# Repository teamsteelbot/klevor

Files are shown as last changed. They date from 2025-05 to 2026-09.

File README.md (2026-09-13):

# Klevor

> [!NOTE]
> Este repositorio corresponde a nuestra participación en la World Robot Olympiad 2025. Si buscas información sobre nuestra participación en la World Robot Olympiad 2026 con V-Titan, el robot del Team Voltimor, visita el repositorio [**vtitan**](https://github.com/teamvoltimor/vtitan).

> [!IMPORTANT]
> If you want to access this content in English, click [**here**](README-en.md)

<p align="center">
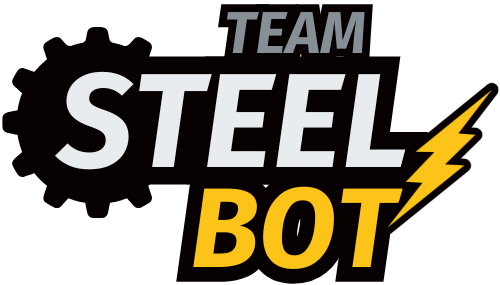
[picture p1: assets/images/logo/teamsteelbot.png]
Logo del Equipo
    
    <br>
    <i>Logo del Equipo</i>
</p>

Bienvenidos al repositorio de Klevor, el robot del Team Steel Bot, que compite en la World Robot Olympiad 2025 en la categoría Futuros Ingenieros. Aquí encontrarás toda la información sobre el robot, incluyendo su código, modelos 3D, esquemas y documentación.

## ¿Cómo acceder a la documentación?

Actualmente, toda la documentación oficial se encuentra tanto en [GitHub Pages](https://klevor.ralvarez.dev), como en el repositorio de [GitHub](https://github.com/teamsteelbot/klevor), recomendamos visualizarla en GitHub Pages, ya que esta documentación fue desarrollada para encajar mejor en este formato. Esta documentación está organizada en varias secciones, cada una de las cuales contiene información específica sobre el robot y su desarrollo.

<p align="center">
	Código QR de la URL de la página web
	<br>
	<i>Código QR de la URL de la página web</i>
</p>

<p align="center">
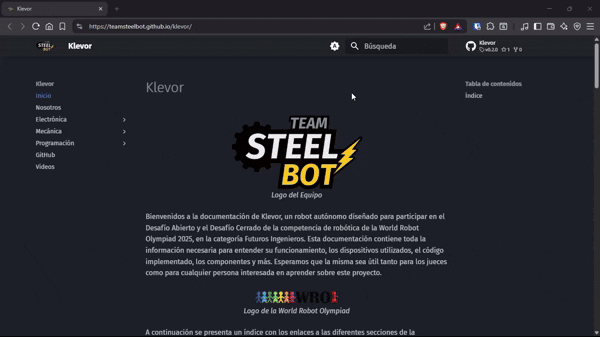
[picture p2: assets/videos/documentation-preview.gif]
Preview de la documentación en GitHub Pages
	
	<br>
	<i>Preview de la documentación en GitHub Pages</i>
</p>

## Estructura de la documentación

Esta documentación es bastante extensa, por lo que decidimos dividir los contenidos de esta documentación en múltiples archivos para facilitar la lectura, los cuales están ubicados en la carpeta `docs`; cabe recalcar que, si un archivo termina en `.es.md` está escrito en español, y si termina en `.en.md` está escrito en inglés.

Ahora bien, la estructura de los archivos es la siguiente:

- En la carpeta `assets` se encuentran las imágenes y videos que utilizamos para este `README`.

- En la carpeta `devices` se encuentra todo el código utilizado por Klevor, dividido en dos carpetas, una para la Raspberry Pi 5, y la otra para la Raspberry Pi Pico 2 W.

- En la carpeta `docs`, como ya se ha mencionado, se encuentra todo lo documentado sobre Klevor, dividido en 3 secciones, la electrónica, la mecánica, la programación, además de estas secciones, también contamos con algunos archivos que detallan, por ejemplo, el software utilizado, los "gadgets" o herramientas que utilizamos, cómo nos pueden contactar, y demás, **estos archivos están listados al final del índice**.

- En la carpeta `models` se encuentran todos los modelos de las piezas 3d que fueron impresas para Klevor, esta carpeta está dividida para los planos de las piezas, y el archivo para imprimirlas, además de, estar organizadas por cada prototipo.

- En la carpeta `schemes` están los diagramas de flujo, y los diagramas de conexiones, además de esto, se incluyeron unos diagramas que explican cómo funciona el sistema de comunicación entre los componentes de Klevor y como se procesan en la Raspberry Pi.

- En la carpeta `t-photos` están las fotos del equipo.

- En la carpeta `v-photos` están las fotos de Klevor.

## Índice 

1. **[Sobre Nosotros](docs/about.es.md)**
2. **Electrónica**
	1. Componentes
		1. [Componentes Previos](docs/electronic/components/previous.es.md)
		2. [Componentes Actuales](docs/electronic/components/current.es.md)
		3. [Componentes Futuros](docs/electronic/components/future.es.md)
	2. Diagramas
		1. [Diagramas de Conexiones](docs/electronic/diagrams/wiring.es.md)
3. **Mecánica**
	1. Piezas
		1. Piezas Comunes
			1. [Piezas Comunes Previas](docs/mechanical/parts/common/previous.es.md)
			2. [Piezas Comunes Actuales](docs/mechanical/parts/common/current.es.md)
		2. [Piezas del Prototipo 1](docs/mechanical/parts/prototype1.es.md)
		3. [Piezas del Prototipo 2](docs/mechanical/parts/prototype2.es.md)
		4. [Piezas del Prototipo 3](docs/mechanical/parts/prototype3.es.md)
		5. [Piezas del Prototipo 4](docs/mechanical/parts/prototype4.es.md)
	2. Prototipos
		1. [Prototipo 1](docs/mechanical/prototypes/prototype1.es.md)
		2. [Prototipo 2](docs/mechanical/prototypes/prototype2.es.md)
		3. [Prototipo 3](docs/mechanical/prototypes/prototype3.es.md)
		4. [Prototipo 4](docs/mechanical/prototypes/prototype4.es.md)
4. **Programación**
	1. Lenguajes de Programación
		1. [Lenguajes de Programación Previos](docs/programming/languages/previous.es.md)
		2. [Lenguajes de Programación Actuales](docs/programming/languages/current.es.md)
		3. [Lenguajes de Programación Futuros](docs/programming/languages/future.es.md)
	2. Librerías
		1. Legado:
		   1. [Librerías de CircuitPython](docs/programming/libraries/legacy/circuit-python.es.md)
		2. [Librerías de Python](docs/programming/libraries/python.es.md)
	3. Diagramas
		1. [Diagramas de Flujo](docs/programming/diagrams/flowcharts.es.md)
	4. [Glosario de Términos](docs/programming/glossary.es.md)
	5. Guías
		1. Legado 
			1. [Guía de MicroPython](docs/programming/guides/legacy/micro-python.es.md)
			2. [Guía de CircuitPython](docs/programming/guides/legacy/circuit-python.es.md)
			3. [Guía de la Raspberry Pi Pico 2 W](docs/programming/guides/legacy/raspberry-pi-pico-2w.es.md)
		2. [Guía de MkDocs](docs/programming/guides/mkdocs.es.md)
		3. [Guía de TinyGo](docs/programming/guides/tinygo.es.md)
		4. [Guía de la Raspberry Pi 5](docs/programming/guides/raspberry-pi-5.es.md)
		5. [Guía de la Raspberry Pi Pico 2 W](docs/programming/guides/raspberry-pi-pico-2w.es.md)
		6. [Guía de Detección de Objetos](docs/programming/guides/object-detection.es.md)
5. **[GitHub](docs/github.es.md)**
6. **[Vídeos](docs/videos.es.md)**
7. **[Software](docs/software.es.md)**
8. **[Gadgets](docs/gadgets.es.md)**
9. **[Patrocinadores](docs/sponsors.es.md)**
10. **[Contacto](docs/contact.es.md)**

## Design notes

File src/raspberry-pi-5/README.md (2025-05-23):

<h1 id="indice">Índice</h1>

1. [Configuración Básica de la Raspberry Pi](#configuracion-basica-de-la-raspberry-pi)
   1. [Instalación de Raspberry Pi OS](#instalacion-de-raspberry-pi-os) 
   2. [Instalación de la cámara](#instalacion-de-la-camara)
2. [Multiprocesamiento](#multiprocesamiento)
3. [YOLO](yolo/README.md)
4. [Recursos Externos](#recursos-externos)

<h1 id="configuracion-basica-de-la-raspberry-pi">Configuración Básica de la Raspberry Pi</h1>

<h1 id="instalacion-de-raspberry-pi-os">Instalación de Raspberry Pi OS</h1>

1. Descargar la imagen de Raspberry Pi OS desde el sitio oficial: [Raspberry Pi OS](https://www.raspberrypi.com/software/).
2. Grabar la imagen en una tarjeta microSD utilizando un software como Balena Etcher o Raspberry Pi Imager.
3. Insertar la tarjeta microSD en la Raspberry Pi y encenderla.
4. Configurar la Raspberry Pi siguiendo las instrucciones en pantalla, incluyendo la conexión a una red Wi-Fi y la creación de un usuario.
5. Actualizar el sistema operativo ejecutando los siguientes comandos en la terminal:
   ```bash
   sudo apt update
   sudo apt upgrade
   ```
   
<p align="center">
    Raspberry Pi OS
    <br>
    <i>Raspberry Pi OS</i>
</p>

*TIP: Por experiencia propia, recomendamos la configuración de la aplicación oficial de Raspberry Pi para conexión remota, Raspberry Pi Connect, que permite acceder a la Raspberry Pi desde cualquier lugar y sin necesidad de estar conectado a la misma red Wi-Fi [[3](#raspberry-pi-connect)]. En nuestro caso, en reiteradas ocasiones nos permitió de forma remota, a través del modo Remote Shell, eliminar procesos que han producido un crash o han limitado la repuesta de la Raspberry Pi.* 

<h1 id="instalacion-de-la-camara">Instalación de la cámara</h1>

1. Conectar la cámara a la Raspberry Pi utilizando el conector CSI.
2. Probar el correcto funcionamiento de la cámara ejecutando el siguiente comando en la terminal:
   ```bash
   libcamera-hello
   ```
3. Si la cámara funciona correctamente, se mostrará una vista previa de la cámara en la pantalla por unos segundos.

*NOTA: En caso de estar interesado en adquirir algún tipo de Raspberry Pi Camera, se debe comprar un cable aparte dependiendo del proveedor, ya que normalmente estas vienen con el cable para la Raspberry Pi 4, el cual no es el mismo.*

<h1 id="multiprocesamiento">Multiprocesamiento</h1>

<h1 id="recursos-externos">Recursos Externos</h1>

1. *Raspberry Pi OS*. (2025). Raspberry Pi. <a id="raspberry-pi-os">https://www.raspberrypi.com/software/</a>
2. *Getting Started*. (2025). Raspberry Pi. <a id="getting-started">https://www.raspberrypi.com/documentation/getting-started/</a>
3. *Raspberry Pi Connect*. (2025). Raspberry Pi. <a id="raspberry-pi-connect">https://www.raspberrypi.com/documentation/remote-access/raspberry-pi-connect.html</a>
4. Python Software Foundation. (2025). *Multiprocessing*. Python documentation. <a id="multiprocessing">https://docs.python.org/3/library/multiprocessing.html</a>
5. Brownlee, J. (28 de julio de 2022). *Use an Event in the Multiprocessing Pool*. SuperFastPython*. <a id="multiprocessing-pool">https://superfastpython.com/multiprocessing-pool/</a>
6. *Camera*. (2025). Raspberry Pi. <a id="camera">https://www.raspberrypi.com/documentation/computers/camera.html</a>
7. Brownlee, J. (21 de noviembre de 2022). *What is a Multiprocessing Manager*. SuperFastPython. <a id="multiprocessing-manager">https://superfastpython.com/multiprocessing-manager/</a>

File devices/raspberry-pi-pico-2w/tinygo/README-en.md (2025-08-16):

# Code

This folder contains all the code developed in TinyGo for the development of Klevor. It is recommended to use a Raspberry Pi Pico 2 WH (although any microcontroller with TinyGo should work with some adjustments) to run the files.

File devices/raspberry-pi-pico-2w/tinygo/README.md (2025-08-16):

# Código

Esta carpeta tiene todo el código realizado en TinyGo para el desarrollo de Klevor, se recomienda utilizar una Raspberry Pi Pico 2 WH (aunque, cualquier microcontrolador con TinyGo debería de poder funcionar si se realizan ciertos ajustes) para poder ejecutar los archivos.

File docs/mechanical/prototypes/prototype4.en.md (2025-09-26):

# Prototype 4

## Vehicle Photos

<!-- github-only-start -->
<table>
	<tbody>
		<tr>
			<td>
				<p align="center">
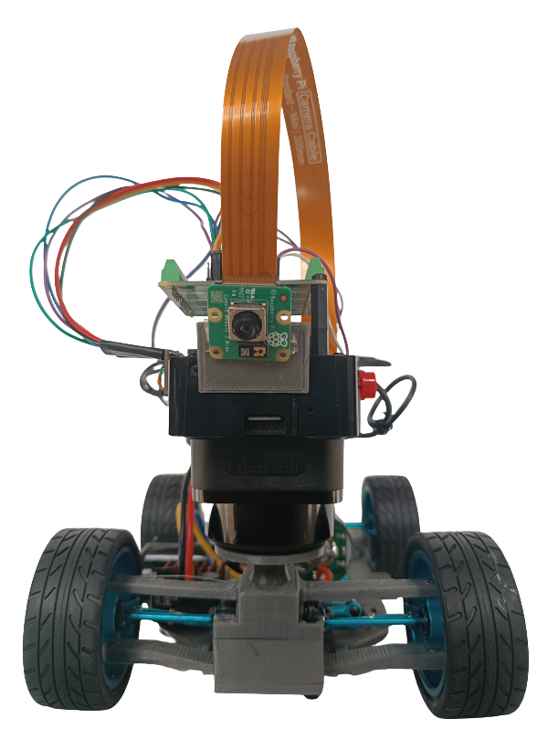
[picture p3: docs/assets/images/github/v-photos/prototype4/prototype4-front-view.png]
Front View
					
					<br>
					<i>Front View</i>
				</p>
			</td>
			<td>
				<p align="center">
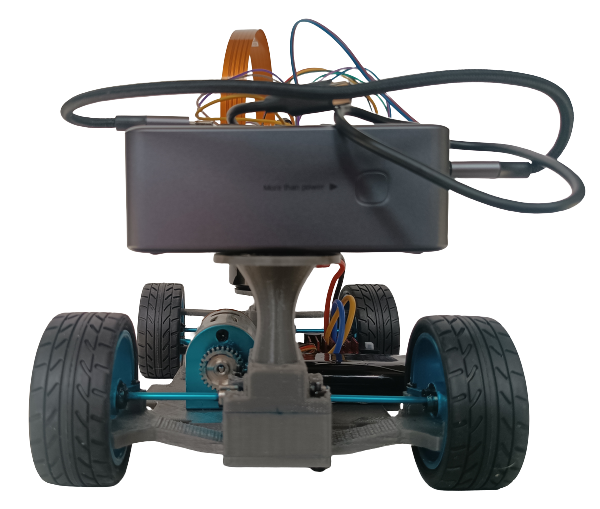
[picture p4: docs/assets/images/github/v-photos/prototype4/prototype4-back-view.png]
Back View
					
					<br>
					<i>Back View</i>
				</p>
			</td>
		</tr>
		<tr>
			<td>
				<p align="center">
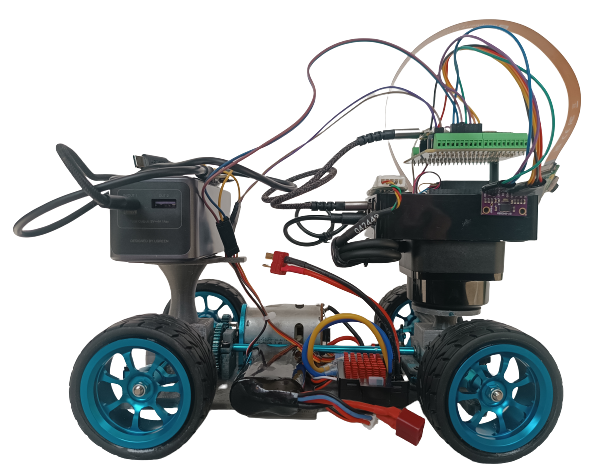
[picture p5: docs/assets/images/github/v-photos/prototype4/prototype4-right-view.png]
Right View
					
					<br>
					<i>Right View</i>
				</p>
			</td>
			<td>
				<p align="center">
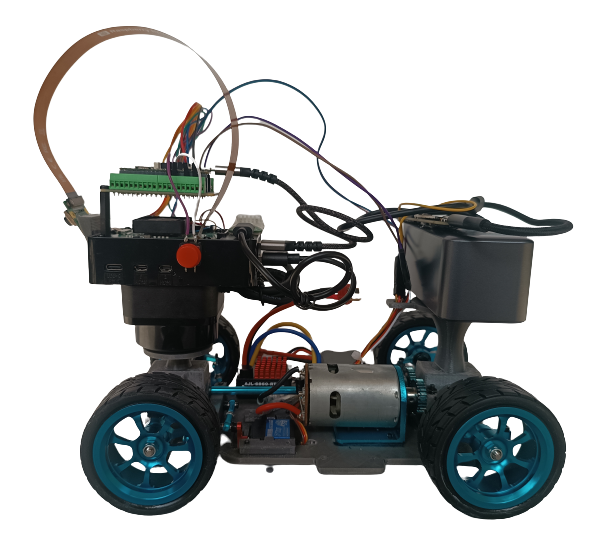
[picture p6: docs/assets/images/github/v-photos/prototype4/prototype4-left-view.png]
Left View
					
					<br>
					<i>Left View</i>
				</p>
			</td>
		</tr>
		<tr>
			<td>
				<p align="center">
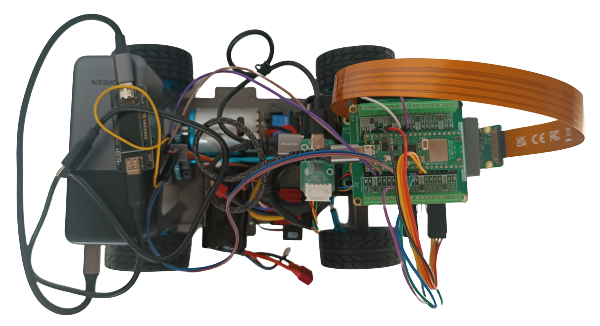
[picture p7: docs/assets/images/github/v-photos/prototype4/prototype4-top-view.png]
Top View
					
					<br>
					<i>Top View</i>
				</p>
			</td>
			<td>
				<p align="center">
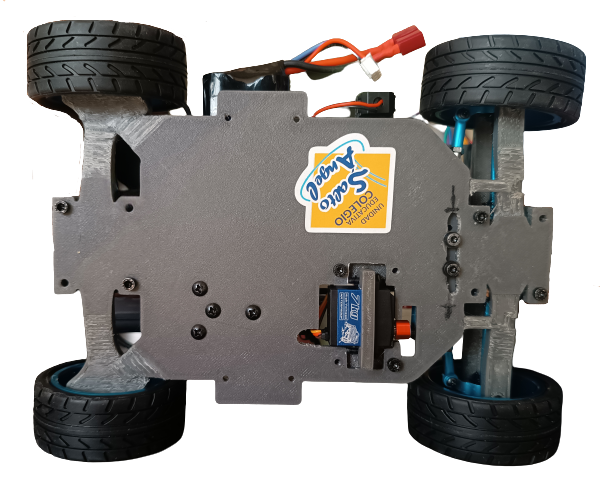
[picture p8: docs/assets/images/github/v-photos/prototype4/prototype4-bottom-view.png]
Bottom View
					
					<br>
					<i>Bottom View</i>
				</p>
			</td>
		</tr>
	</tbody>
</table>
<!-- github-only-end -->

<!-- mkdocs-only-start
<div class="vehicle-views-container">
    <div class="hcenter">
        <img src="/assets/images/github/v-photos/prototype4/prototype4-front-view.png" 
alt="Front View" class="vehicle-view-image">
        <i>Front View</i>
    </div>
    <div class="hcenter">
        <img src="/assets/images/github/v-photos/prototype4/prototype4-back-view.png" 
alt="Back View" class="vehicle-view-image">
        <i>Back View</i>
    </div>
    <div class="hcenter">
        <img src="/assets/images/github/v-photos/prototype4/prototype4-right-view.png" 
alt="Right View" class="vehicle-view-image">
        <i>Right View</i>
    </div> 
    <div class="hcenter">
        <img src="/assets/images/github/v-photos/prototype4/prototype4-left-view.png" 
alt="Left View" class="vehicle-view-image">
        <i>Left View</i>
    </div>
    <div class="hcenter">
        <img src="/assets/images/github/v-photos/prototype4/prototype4-top-view.png"
alt="Top View" class="vehicle-view-image">
        <i>Top View</i>
    </div>
    <div class="hcenter">
        <img src="/assets/images/github/v-photos/prototype4/prototype4SS-bottom-view.png" 
alt="Bottom View" class="vehicle-view-image">
        <i>Bottom View</i>
    </div>
</div>
mkdocs-only-end -->

## Introduction

This Klevor prototype is the fruit of labor focused on improving its efficiency to complete the challenges that this WRO edition provides. Across these upgrades, we prioritized the mechanical engineering to overcome the limitations from previous prototypes and optimized its performance.

From the very first concept, Klevor was born with a clear idea. It was established that its main processor would be a Raspberry Pi 5, a decision that made us able to add Artificial Intelligence capabilities with an AI HAT+ and a Raspberry Pi Cam 3 to detect precisely the object. For the navigation, we used the RPLiDAR C1 sensor, which provides a detection from multiple angles.

Klevor uses a 4x4 traction system to maximize the strength and control. Also, we implemented a Ackermann steering system, which optimizes the wheels' turning angle. This system, known for its use in automobiles, aligns the turning wheels in a way that all of them turn around a common point, which mainly improves the stability during the turns.

To build our robot's unique parts, such as the bases and supports, we used a design program named Fusion360. With this program we were able to create every single piece from scratch and then 3D print them. Thanks to this, we could have less margin for errors, or correct quicker, achieving a more optimal design.

Thorought this prototype's explanation, we will detail in Klevor's trayectory, starting from the component's first ideas to the creation of solutions that helped with our problems related to power, traction and weight.

Another fundamental part for our robot is its crossing system, which consists of a servomotor ([INJORA 7 kg 2065](../../electronic/components/current.en.md#injora-7-kg-2065-micro-servo)) which is connected to our "Ackermann" system that works by connecting both wheels to a steering or "trapezoid system". The servomotor moves some bars that are connected to the steering knuckles, thus allowing that one of the steering knuckles to be pushed to one side by the movement of the servomotor and in turn, pull the other wheel to the other side. Due to the angles of the trapezoid, this causes that the interior wheel to turn more than the outer one.

To operate, the wheels are connected to a steering knuckle, then to a "shaft" or "half-shaft" that passes through the knuckle and joins the wheel so that it turns; the shaft turns while it is next to the differential.

<!-- github-only-start -->
<p align="center">
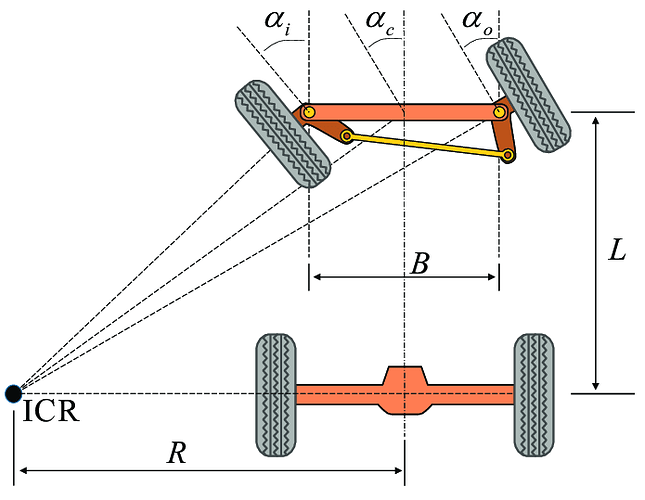
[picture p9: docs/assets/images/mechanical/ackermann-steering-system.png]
Ackermann System
    
    <br>
    <i>Ackermann System</i>
</p>
<!-- github-only-end -->

<!-- mkdocs-only-start
<div class="hcenter">
    <img src="/assets/images/mechanical/ackermann-steering-system.png" 
alt="Ackermann System" class="mechanical-image">
    <i>Ackermann System</i>
</div>
mkdocs-only-end -->

This diagram provides a clearer example on how this system works. We'll describe the meaning of each term below:

- **ICR** (Instantaneous Center of Rotation): It's the point around which the front axle is rotating.

- **R**: It's the vehicle's turning radius, measured from the ICR to the center of the rear axle.

- **L**: It's the distance between the front and rear axle, or, the transmission shaft's length.

- **B**: It's the distance between the sterring knuckles (The piece on which the wheel goes and is connected to the steering).

- **a(i)**: Is the turning angle of our inner wheel compared to the curve.

- **a(o)**: Is the angle of our outer wheel with respect to the turn.

This ilustrates better the steering geometry that allows for the front wheels to turn in different angles and, at the same time, achieving a more efficient turning.

## Changes

To improve Klevor's performance and efficiency, we implemented multiple changes in its design. These upgrades are focused in upgrading aspects such as traction, motor power and weight distribution.

- New chassis and wheels

Klevor's new chassis was designed specifically to integrate the new components, assuring that each of them has the adequate space for its proper functioning. The main reason for this redesign was the incorporation for new aluminum wheels. Unlike previous prototypes, these wheels have a larger diameter and are wider, their tire rubber is also thicker and smoother. This design provides a better grip on flat surfaces, correcting traction problems that we had previously.

- Bigger torque and motor efficiency

We replaced the previous motor (INJORA 48T) with another motor that has more torque. This change allows us to use the motor's speed to its fullest, which is worth noting, since it can go above the 20,000 RPM, without the need of a system to reduce the revolutions per minute (RPM).

- Weight reduction

Another significant change is that we substituted the power supply. In previous prototypes, we used a power bank and weighted almost 600g (Shargeek Storm 2), which limitated our ability to modify the design. Now, with a new power bank weighing just 350g, we have achieved a considerable weight reduction. This upgrade allows us to have more freedom to optimize the chassis without having to worry about the robot's weight.

## How did we design Klevor?

First of all, we think, "What do we need to get an efficient robot?" Starting from there, we established a clear idea, a robot programmed with a Raspberry Pi 5, which would allow us to use a Raspberry Pi AI HAT+ and train our Raspberry Pi Cam 3 through artificial intelligence, which would definitely help us have a better performance in the Closed Challenge, and, to make sure Klevor detects the objects surrounding it, capable to detect with a wide range, we decided to use the RPLiDAR C1 since our second prototype. Mechanically wise, we always wanted to use a 4x4 traction system and Ackermann's steering geometry.

To make everything work, we thought about every component we wanted to use, to build mountings and supports for them, we decided that it was a good idea to 3D print these supports, more specifically, we used PETG filament, which is very resistant, affordable and easy to come by, which would allow us to make multiple tests.

All of our 3D printed parts were created from scratch, designed in a program called Fusion360, this same program was a huge help in multiple aspects, for example, we could simulate the dimensions from each component in the program and then afterwards create multiple designs for the chassis.

## Problems and solutions during developmennt

Even though we had a solid idea as to how we wanted to shape Klevor, we had a few inconveniences during the building process, for Klevor's first 3 prototypes we decided to use a Motor Injora 48T, which we thought it could move the whole robot, even thought it was a 20000 RPM motor, it didn't have enough torque to move Klevor, so we created a RPM reduction system, according to these principles:

**When a smaller pinion (impulsor) moves a bigger pinion (impulsed), the speed decreases and the torque increases.**

**When a bigger pinion (impulsor) moves a smaller pinion (impulsed), the torque decreases and the speed increases.**

**The reduction ratio or transmission ratio can be calculated with the following formula:**

<!-- github-only-start -->
<p align="center">
	Gear Ratio Formula
	<br>
	<i>Gear Ratio Formula</i>
</p>
<!-- github-only-end -->

<!-- mkdocs-only-start
<div class="hcenter">
	<img src="/assets/images/mechanical/gear-ratio-formula.png" alt="Gear Ratio Formula" class="mechanical-image">
	<i>Gear Ratio Formula</i>
</div>
mkdocs-only-end -->

This means that, in order to increase the torque, we have to arrange the system in a way that, pinions with less teeth are the ones that move pinions with more teeth, this was the solution to our torque problem.

Afterwards, we had to make Klevor lighter, the reason for this change, were the previously mentioned, new wheels, because the old wheels' rims were 3D printed, which in turn, wore them down quickly. The newer wheels had an aluminum rim and a thicker rubber, which in tunr, would make Kleovr exceed the reglamentary weight limit established by the WRO, what we did to solve this problem and to make the robot faster as well, was to change the motor, with one that had 20000 RPM, but with enough torque, which made the RPM reduction system obsolete.

Another issue that was present during Klevor's development was its limited turning angle, which supposed a huge challenge in the game field. To correct it, we modified the shape of the Ackermann steering system, which is composed of two direction knuckles and the shaft that unifies them, by adjusting the position and angle of these components, we increased Klevor's turning angle significantly.

## Bill Of Materials

| Component |  Unit  | Cost per Unit ($)  | Total ($) |
|---|---|---|---|
| [Raspberry Pi 5](https://www.canakit.com/raspberry-pi-5-16gb.html) | 1 | 120.00 | 120.00 |
| [Raspberry Pi AI HAT+](https://www.canakit.com/raspberry-pi-ai-hat-with-case.html) | 1 | 139.95 | 139.95 |
| [Micro SD 512GB](https://www.amazon.com/dp/B0C1Q79X3P) | 1 | 54.99 | 54.99 |
| [RPLiDAR C1](https://www.amazon.com/dp/B0CNXLJJ61) | 1 | 75.90 | 75.90 |
| [Raspberry Pi Camera Module 3 Wide](https://www.canakit.com/raspberry-pi-camera-module-3.html) | 1 | 37.95 | 37.95 |
| [Case para la Raspberry Pi Camera Module 3](https://www.amazon.com/dp/B09TNG4V55) | 1 | 5.99 | 5.99 |
| [Cable para la cámara de la Raspberry Pi 5 de 50cm](https://www.amazon.com/dp/B0D3YWTNF8) | 1 | 9.79 | 9.79 |
| [Raspberry Pi Pico 2WH](https://www.amazon.com/dp/B0F4W9J5CC) | 1 | 14.99 | 14.99 |
| [Raspberry Pi Pico 2WH Breakout Board](https://www.amazon.com/dp/B0BFB53Y2N) | 1 | 11.95 | 11.95 |
| [URGENEX 3000mAh Battery](https://www.amazon.com/dp/B0CYNVSN7W) | 1 | 26.99 | 26.99 |
| [Giroscopio BNO085](https://www.amazon.com/dp/B0CDGZMLPP) | 1 | 18.59 | 18.59 |
| [INJORA 7Kg 2065 Servo](https://www.amazon.com/dp/B0BLBMVYCW) | 1 | 17.98 | 17.98 |
| [60A Brushed ESC para 2-3s LiPo y motor 540](https://www.amazon.com/dp/B0F9Y6CMC8) | 1 | 15.98 | 15.98 |
| [Motor 540 y disipador de calor de aluminio](https://www.amazon.com/dp/B0995W966Z) | 1 | 19.39 | 19.39 |
| [UGREEN Power Bank 12000mAh 100W PD PPS](https://www.amazon.com/dp/B0CXJ1F1M7) | 1 | 49.99 | 49.99 |
| [Aluminium Alloy Front & Rear Steering Knuckle Hub Base](https://www.amazon.com/dp/B09XW246FQ) | 1 | 17.99 | 17.99 |
| [RC Car Metal Differential Kit 1/18](https://www.amazon.com/dp/B08GHC4D5M) | 1 | 21.98 | 21.98 |
| [USB-C QC PD3.0 Trigger Board Module Type-C](https://www.amazon.com/dp/B0DRJWBG7G) | 1 | 16.99 | 16.99 |
| [Llantas de metal con buje de metal de 0.472 pulg](https://www.amazon.com/dp/B0BP2W7W59) | 1 | 20.99 | 20.99 |
| [Copa diferencial de aleación de aluminio y junta de eje de transmisión](https://www.amazon.com/dp/B09P1QV29K) | 1 | 10.99 | 10.99 |
| [20 rodamientos de bolas MR128-2RS](https://www.amazon.com/dp/B09P1QV29K) | 1 | 9.29 | 9.29 |
| [Uxcell 0.276 in I.D. Rodamientos de bolas en miniatura](https://www.amazon.com/dp/B07XYPLPFL) | 1 | 8.49 | 8.49 |
| [Smays Cable USB C de 240 W, cable corto de 1 pie C a C](https://www.amazon.com/dp/B0CYT6KQTR) | 1 | 7.99 | 7.99 |
| [Hobbypark Adaptador hexagonal de rueda de aluminio](https://www.amazon.com/dp/B07D67VMDN) | 1 | 9.97 | 9.97 |
| [6 piezas ajustables de aluminio Hobbypark enlace servo](https://www.amazon.com/dp/B01MQOA4CH) | 1 | 15.95 | 15.95 |
| [6 HobbyPark Metal Diff diferencial engranaje principal 42T y piñón motor 27T](https://www.amazon.com/dp/B07FS5RGLS) | 1 | 11.98 | 11.98 |
| [Cable micro USB corto de 1 pie [paquete de 3]](https://www.amazon.com/dp/B07FS5RGLS) | 1 | 6.99 | 6.99 |

**Component Cost Total: $780.03**

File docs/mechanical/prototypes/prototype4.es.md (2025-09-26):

# Prototipo 4 {:#prototype4}

## Fotos del vehículo

<!-- github-only-start -->
<table>
	<tbody>
		<tr>
			<td>
				<p align="center">
					Vista delantera del prototipo 4
					<br>
					<i>Vista delantera del prototipo 4</i>
				</p>
			</td>
			<td>
				<p align="center">
					Vista trasera del prototipo 4
					<br>
					<i>Vista trasera del prototipo 4</i>
				</p>
			</td>
		</tr>
		<tr>
			<td>
				<p align="center">
					Vista derecha del prototipo 4
					<br>
					<i>Vista derecha del prototipo 4</i>
				</p>
			</td>
			<td>
				<p align="center">
					Vista izquierda del prototipo 4
					<br>
					<i>Vista izquierda del prototipo 4</i>
				</p>
			</td>
		</tr>
		<tr>
			<td>
				<p align="center">
					Vista superior del prototipo 4
					<br>
					<i>Vista superior del prototipo 4</i>
				</p>
			</td>
			<td>
				<p align="center">
					Vista inferior del prototipo 4
					<br>
					<i>Vista inferior del prototipo 4</i>
				</p>
			</td>
		</tr>
	</tbody>
</table>
<!-- github-only-end -->

<!-- mkdocs-only-start
<div class="vehicle-views-container">
    <div class="hcenter">
        <img src="/assets/images/github/v-photos/prototype4/prototype4-front-view.png" 
alt="Vista delantera" class="vehicle-view-image">
        <i>Vista delantera</i>
    </div>
    <div class="hcenter">
        <img src="/assets/images/github/v-photos/prototype4/prototype4-back-view.png" 
alt="Vista Trasera" class="vehicle-view-image">
        <i>Vista trasera</i>
    </div>
    <div class="hcenter">
        <img src="/assets/images/github/v-photos/prototype4/prototype4-right-view.png" 
alt="Vista derecha" class="vehicle-view-image">
        <i>Vista derecha</i>
    </div>
    <div class="hcenter">
        <img src="/assets/images/github/v-photos/prototype4/prototype4-left-view.png" 
alt="Vista izquierda" class="vehicle-view-image">
        <i>Vista izquierda</i>
    </div>
    <div class="hcenter">
        <img src="/assets/images/github/v-photos/prototype4/prototype4-top-view.png"
alt="Vista superior" class="vehicle-view-image">
        <i>Vista superior</i>
    </div>
    <div class="hcenter">
        <img src="/assets/images/github/v-photos/prototype4/prototype4SS-bottom-view.png" 
alt="Vista inferior" class="vehicle-view-image">
        <i>Vista inferior</i>
    </div>
</div>
mkdocs-only-end -->

## Introducción

Este prototipo de Klevor es el fruto de un arduo trabajo enfocado en mejorar su eficiencia a la hora de realizar los desafíos que depara esta edición de la WRO. A lo largo de estas mejoras, hemos priorizado la ingeniería mecánica para superar las limitaciones de prototipos anteriores y optimizar su desempeño.

Desde el primer concepto, Klevor fue pensado con una idea clara. Se estableció que su cerebro sería una Raspberry Pi 5, una decisión que nos permitió añadir capacidades de inteligencia artificial con un AI HAT+ y una Raspberry Pi Cam 3 para la detección precisa de objetos. Para la navegación, utilizamos el sensor RPLidar C1, que proporciona una detección en múltiples ángulos.

Klevor utiliza un sistema de tracción 4x4 para maximizar la fuerza y el control. Además, implementamos un sistema de cruce Ackermann, que optimiza el ángulo de giro de las ruedas. Este sistema, conocido por su uso en automóviles, alinea las ruedas de dirección de manera que todas giren alrededor de un punto común, lo que principalmente mejora la estabilidad durante los giros.

Para construir las partes únicas de nuestro robot, como las bases y los soportes, usamos un programa de diseño llamado Fusion360. Con este programa, pudimos crear cada pieza desde cero y luego imprimirlas en 3D. Gracias esto, pudimos tener menos margen de error, o corregir más rapido, logrando un diseño óptimo.

A lo largo la explicación de este prototipo, detallaremos el trayecto de Klevor, desde las primeras ideas de sus componentes hasta la creación de soluciones que ayudaron con nuestros problemas de potencia, tracción y peso.

Una parte fundamental para nuestro robot es su sistema de cruce. Es basado en un mecanismo Ackermann, que consiste en que las dos ruedas están conectadas por una dirección o "sistema de trapecio", esto lo que hace es que, mediante una fuerza que haga el cruce (en este caso nuestro servomotor [INJORA 7 kg 2065](../../electronic/components/current.md#injora-7kg-2065-micro-servo))la dirección se mueva y eso hace girar ambas ruedas al mismo lado, debido a la geometría y forma de trapecio que tiene la dirección, las ruedas no giran con el mismo ángulo, sino que, la rueda interna respecto al cruce gira más que la rueda externa.

Las ruedas para funcionar están conectadas a un muñón de dirección, luego a un "palier" o "semieje" que pasa por dentro del muñón y se junta con la rueda para que esta gire, el palier gira mientras está junto al diferencial.

<!-- github-only-start -->
<p align="center">
    Sistema de Ackermann
    <br>
    <i>Sistema de Ackermann</i>
</p>
<!-- github-only-end -->

<!-- mkdocs-only-start
<div class="hcenter">
    <img src="/assets/images/mechanical/ackermann-steering-system.png" 
alt="Sistema de Ackermann" class="mechanical-image">
    <i>Sistema de Ackermann</i>
</div>
mkdocs-only-end -->

En este diagrama se ve un ejemplo más claro de cómo funciona este sistema. Describiremos a continuación el significado de cada término:

- **ICR** (Centro Instantáneo de Rotación): Es el punto alrededor del cual el eje delantero está girando.

- **R**: Es el radio del giro del vehículo, medido desde el ICR hasta el centro del eje trasero.

- **L**: Es la distancia entre el eje delantero y el eje trasero de Klevor, o la distancia de nuestro eje transmisor.

- **B**: Es la distancia entre los muñones de dirección (La pieza en la que va la rueda y se conecta a la dirección).

- **a(i)**: Es el ángulo de giro de nuestra rueda interior respecto a la curva.

- **a(o)**: Es el ángulo de nuestra rueda exterior respecto al giro.

Esto ilustra más la geometría de la dirección que permite que las ruedas delanteras giren en ángulos diferentes y a su vez en la misma dirección, consiguiendo así un giro eficiente.

## Cambios
Para mejorar el rendimiento y la eficiencia de Klevor, hemos implementado varios cambios en su diseño. Estas mejoras se enfocan en optimizar la tracción, la potencia del motor y la distribución del peso.

- Nuevo chasis y ruedas

El nuevo chasis de Klevor fue diseñado específicamente para integrar de manera eficiente los nuevos componentes, asegurando que cada uno tenga el espacio adecuado para su funcionamiento. La principal razón para este rediseño fue la incorporación de nuestras nuevas ruedas de aluminio. A diferencia de los prototipos anteriores, estas ruedas tienen un diámetro y ancho mayores, y cuentan con un caucho más grueso y liso. Este diseño le proporciona a Klevor un mejor agarre en superficies planas, corrigiendo problemas de tracción que teníamos anteriormente.

- Mayor torque y eficiencia motriz

Hemos reemplazado el motor anterior (INJORA 48T) por uno con mayor torque. Este cambio nos permite aprovechar al máximo la velocidad del motor, que alcanza las 20,000 RPM, sin necesidad de un sistema para reducir las revoluciones por minuto (RPM).

- Reducción de peso

Otro cambio significativo es la sustitución de la fuente de alimentación. En prototipos anteriores, utilizábamos un power bank de casi 600g (Shargeek Storm 2), lo que limitaba las modificaciones de diseño. Ahora, con un nuevo power bank de solo 350g, hemos logrado una reducción considerable del peso. Esta mejora nos dio más libertad para optimizar el chasis sin tener que preocuparnos tanto por el peso total del robot.

## ¿Cómo diseñamos a Klevor?

Primeramente pensamos en ¿qué necesitamos para tener un robot eficiente? A partir de eso, se estableció una idea clara, un robot programado en una Rasperry Pi 5, lo que nos permitiría posteriormente usar un Raspberry PI AI HAT+ y entrenar a nuestra Raspberry Pi Cam 3 mediante inteligencia artificial, lo que definitivamente nos ayudaría a tener un mejor rendimiento en el desafío cerrado, y para que Klevor detecte los objetos a su alrededor, sensores capaces de detectar en varios ángulos, es por eso que desde nuestro segundo prototipo empezamos a usar el RPLidar C1. En cuanto a mecánica, desde el principio quisimos usar un sistema de tracción 4x4, y un sistema de cruce Ackermann.

Para lograr hacer que todo esto funcionase, pensamos en cada componente que teníamos que usar, para construir bases y soportes para los mismos, decidimos que una buena opción era imprimir estas piezas con una impresora 3D, más específicamente con un filamento tipo PTEG, el cual es bastante resistente, no muy costoso y fácil de conseguir, lo que nos permitiría hacer varias pruebas.

Todas nuestras piezas impresas fueron creadas desde 0, diseñadas en un programa de diseño llamado Fusion360, el cual fué de ayuda en varios aspectos, ya que podíamos simular las dimensiones de cada componente en el software y así posteriormente crear diferentes diseños para el chasis.

## Problemas y soluciones durante el desarrollo
A pesar de tener una base sólida acerca de lo que queríamos para construir a Klevor, se nos presentaron varios inconvenientes durante la construcción del mismo, para el primer prototipo de Klevor decidimos usar un Motor Injora 48T, que pensabamos íba a mover todo nuestro robot, a pesar de tener 20000 RPM, este no contaba con el torque suficiente para hacer a Klevor moverse, por lo que ideamos un sistema reductor de RPM, basándonos en los siguientes principios:

**Cuando un piñón más pequeño (impulsor) mueve uno más grande (impulsado), la velocidad disminuye y el torque aumenta.**

**Cuando uno más grande mueve a uno más pequeño, la velocidad aumenta y el torque disminuye.**

**La relación de transmisión o relación de reducción se calcula con la siguiente fórmula:**

<p align="center">
	Gear Ratio Formula
	<br>
	<i>Gear Ratio Formula</i>
</p>

Esto significa que para aumentar el torque, tenemos que hacer que los piñones con menos dientes muevan a los piñones con más dientes, esto fué la solución para el problema de torque de nuestro robot.

Posteriormente tuvimos que hacer que Klevor fuese más liviano, la razón era el cambio de ruedas antes mencionado, ya que los rines de las que fueron utilizadas en prototipos anteriores eran impresas en 3D, lo que hacía que se desgastasen rápido. El nuevo modelo de rueda que estamos usando tiene un rin hecho de aluminio y un caucho mas grueso, lo que a su vez excedería el peso máximo establecido por la WRO, lo que hicimos para solucionar este problema y a la vez añadir más velocidad a Klevor fue cambiar el motor, uno que también cuenta con 20000 RPM, pero con torque suficiente, lo que significa que el sistema reductor antes mencionado fué descartado. 

Otra falla que presentó Klevor durante su desarrollo fué que el ángulo de giro de las ruedas era limitado, lo que suponía una dificultad a la hora de cruzar. Para corregirlo, modificamos la forma del trapecio de dirección del sistema de cruce Ackermann, el cual está compuesto por los dos brazos de dirección y la barra de acoplamiento que los une, al ajustar la posición y el ángulo de estos componentes, logramos que el ángulo de giro de Klevor incrementara significativamente.

## Lista de Materiales {:#materials-list}

| Componente | Unidad | Costo por Unidad ($) | Total ($) |
|---|---|---|---|
| [Raspberry Pi 5](https://www.canakit.com/raspberry-pi-5-16gb.html) | 1 | 120.00 | 120.00 |
| [Raspberry Pi AI HAT+](https://www.canakit.com/raspberry-pi-ai-hat-with-case.html) | 1 | 139.95 | 139.95 |
| [Micro SD 512GB](https://www.amazon.com/dp/B0C1Q79X3P) | 1 | 54.99 | 54.99 |
| [RPLiDAR C1](https://www.amazon.com/dp/B0CNXLJJ61) | 1 | 75.90 | 75.90 |
| [Raspberry Pi Camera Module 3 Wide](https://www.canakit.com/raspberry-pi-camera-module-3.html) | 1 | 37.95 | 37.95 |
| [Case para la Raspberry Pi Camera Module 3](https://www.amazon.com/dp/B09TNG4V55) | 1 | 5.99 | 5.99 |
| [Cable para la cámara de la Raspberry Pi 5 de 50cm](https://www.amazon.com/dp/B0D3YWTNF8) | 1 | 9.79 | 9.79 |
| [Raspberry Pi Pico 2WH](https://www.amazon.com/dp/B0F4W9J5CC) | 1 | 14.99 | 14.99 |
| [Raspberry Pi Pico 2WH Breakout Board](https://www.amazon.com/dp/B0BFB53Y2N) | 1 | 11.95 | 11.95 |
| [URGENEX 3000mAh Battery](https://www.amazon.com/dp/B0CYNVSN7W) | 1 | 26.99 | 26.99 |
| [Giroscopio BNO085](https://www.amazon.com/dp/B0CDGZMLPP) | 1 | 18.59 | 18.59 |
| [INJORA 7Kg 2065 Servo](https://www.amazon.com/dp/B0BLBMVYCW) | 1 | 17.98 | 17.98 |
| [60A Brushed ESC para 2-3s LiPo y motor 540](https://www.amazon.com/dp/B0F9Y6CMC8) | 1 | 15.98 | 15.98 |
| [Motor 540 y disipador de calor de aluminio](https://www.amazon.com/dp/B0995W966Z) | 1 | 19.39 | 19.39 |
| [UGREEN Power Bank 12000mAh 100W PD PPS](https://www.amazon.com/dp/B0CXJ1F1M7) | 1 | 49.99 | 49.99 |
| [Aluminium Alloy Front & Rear Steering Knuckle Hub Base](https://www.amazon.com/dp/B09XW246FQ) | 1 | 17.99 | 17.99 |
| [RC Car Metal Differential Kit 1/18](https://www.amazon.com/dp/B08GHC4D5M) | 1 | 21.98 | 21.98 |
| [USB-C QC PD3.0 Trigger Board Module Type-C](https://www.amazon.com/dp/B0DRJWBG7G) | 1 | 16.99 | 16.99 |
| [Llantas de metal con buje de metal de 0.472 pulg](https://www.amazon.com/dp/B0BP2W7W59) | 1 | 20.99 | 20.99 |
| [Copa diferencial de aleación de aluminio y junta de eje de transmisión](https://www.amazon.com/dp/B09P1QV29K) | 1 | 10.99 | 10.99 |
| [20 rodamientos de bolas MR128-2RS](https://www.amazon.com/dp/B09P1QV29K) | 1 | 9.29 | 9.29 |
| [Uxcell 0.276 in I.D. Rodamientos de bolas en miniatura](https://www.amazon.com/dp/B07XYPLPFL) | 1 | 8.49 | 8.49 |
| [Smays Cable USB C de 240 W, cable corto de 1 pie C a C](https://www.amazon.com/dp/B0CYT6KQTR) | 1 | 7.99 | 7.99 |
| [Hobbypark Adaptador hexagonal de rueda de aluminio](https://www.amazon.com/dp/B07D67VMDN) | 1 | 9.97 | 9.97 |
| [6 piezas ajustables de aluminio Hobbypark enlace servo](https://www.amazon.com/dp/B01MQOA4CH) | 1 | 15.95 | 15.95 |
| [6 HobbyPark Metal Diff diferencial engranaje principal 42T y piñón motor 27T](https://www.amazon.com/dp/B07FS5RGLS) | 1 | 11.98 | 11.98 |
| [Cable micro USB corto de 1 pie [paquete de 3]](https://www.amazon.com/dp/B07FS5RGLS) | 1 | 6.99 | 6.99 |

**Total para los Componentes: $780.03**

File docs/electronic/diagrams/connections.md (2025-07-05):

# Diagramas de Conexiones {:#connections-diagrams}

## Prototipo 1 {:#prototype1}

<div class="center">
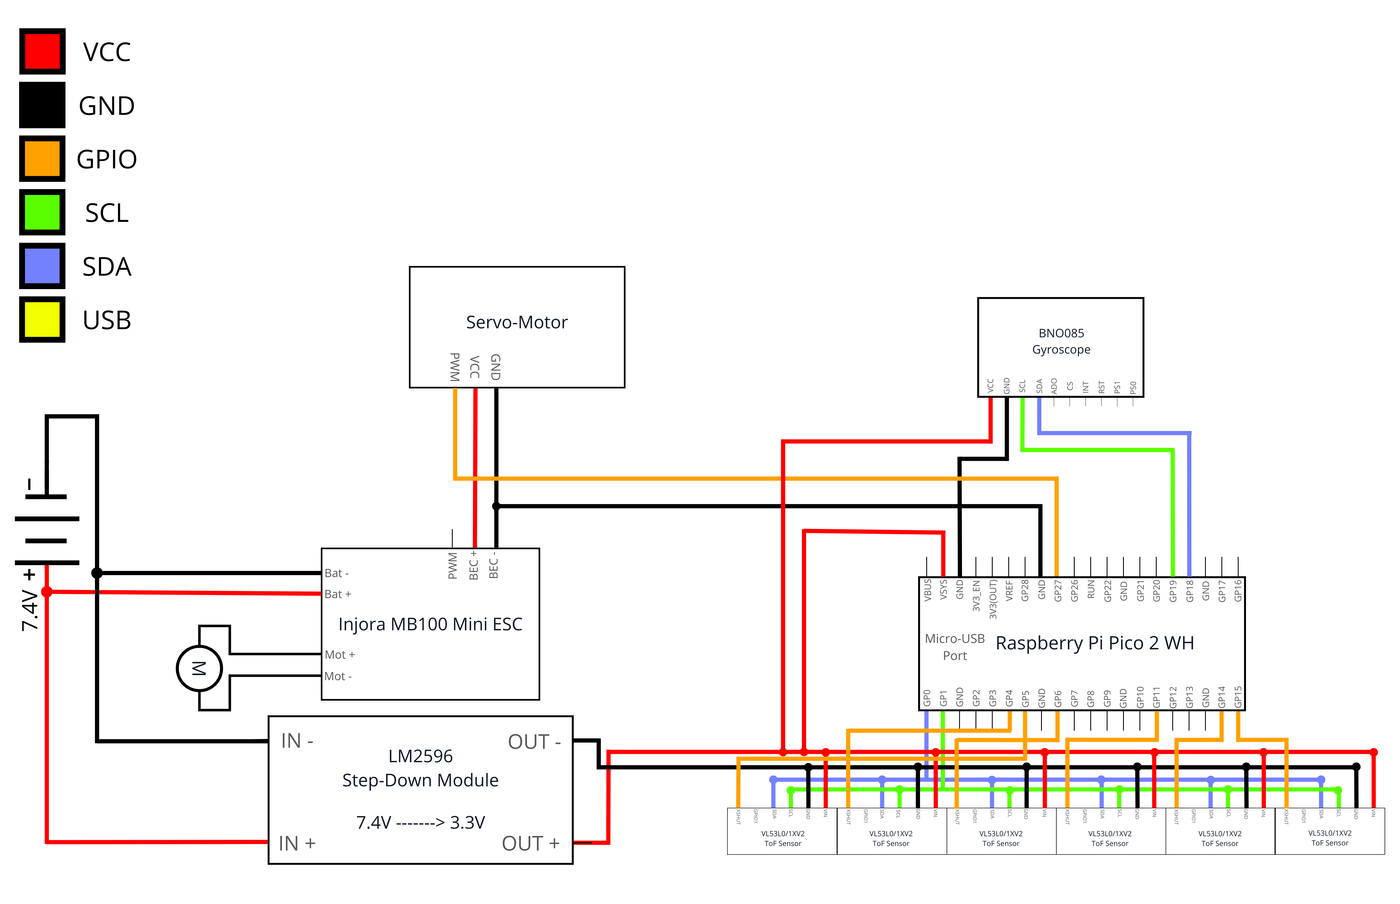
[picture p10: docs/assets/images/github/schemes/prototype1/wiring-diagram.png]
Diagrama de Conexiones del Prototipo 1
    
    <i>Diagrama de Conexiones del Prototipo 1</i>
</div>

## Prototipo 2 {:#prototype2}

<div class="center">
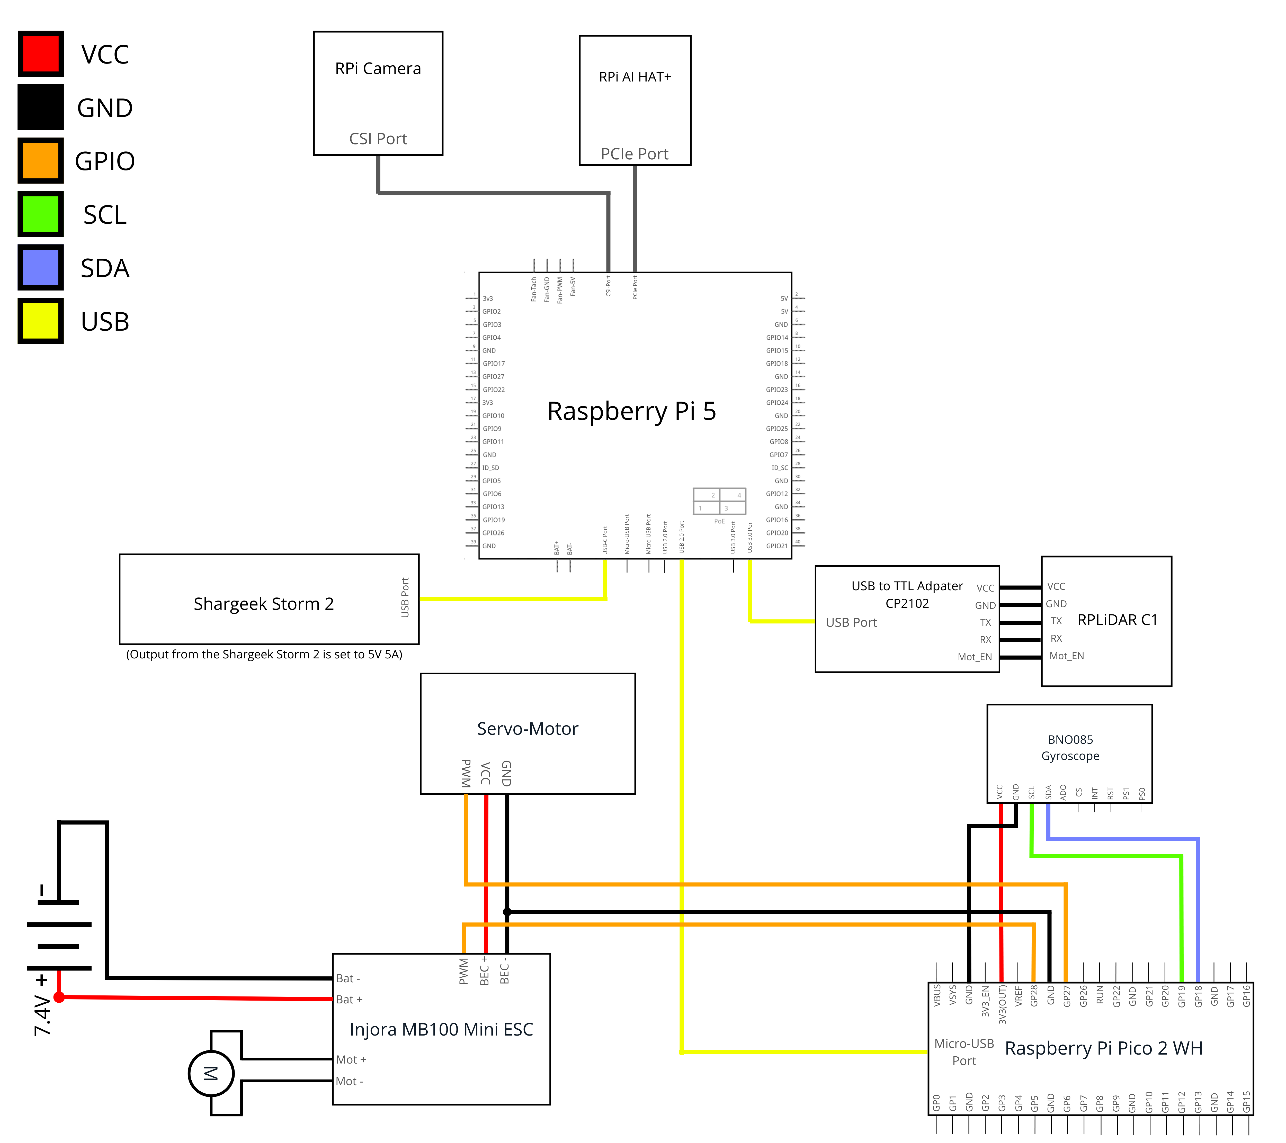
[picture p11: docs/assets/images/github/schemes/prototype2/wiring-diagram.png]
Diagrama de Conexiones del Prototipo 2
    
    <i>Diagrama de Conexiones del Prototipo 2</i>
</div>

## Prototipo 3 {:#prototype3}

<div class="center">
    Diagrama de Conexiones del Prototipo 3
    <i>Diagrama de Conexiones del Prototipo 3</i>
</div>

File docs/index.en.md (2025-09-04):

# Home

<!-- github-only-start -->
<p align="center">
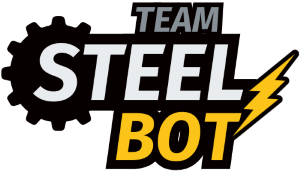
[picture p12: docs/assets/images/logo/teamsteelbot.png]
Team Steel Bot's Logo
	
	<br>
	<i>Team Steel Bot's Logo</i>
</p>
<!-- github-only-end -->

<!-- mkdocs-only-start
<div class="hcenter">
    <img src="/assets/images/logo/teamsteelbot.png" alt="Team Steel Bot's Logo" 
class="logo--team">
    <i>Team Steel Bot's Logo</i>
</div>
mkdocs-only-end -->

Welcome to Klevor's documentation, an autonomous robot designed to participate on the World Robot Olympiad 2025, in the Future Engineers category. This documentation aims to offer all the necessary info to understand how Klevor works, the different devices involved, the source code and more. We hope that it is as useful as possible for both the judges and anyone that is interested in the project.

<!-- github-only-start -->
<div>
	<p align="center">
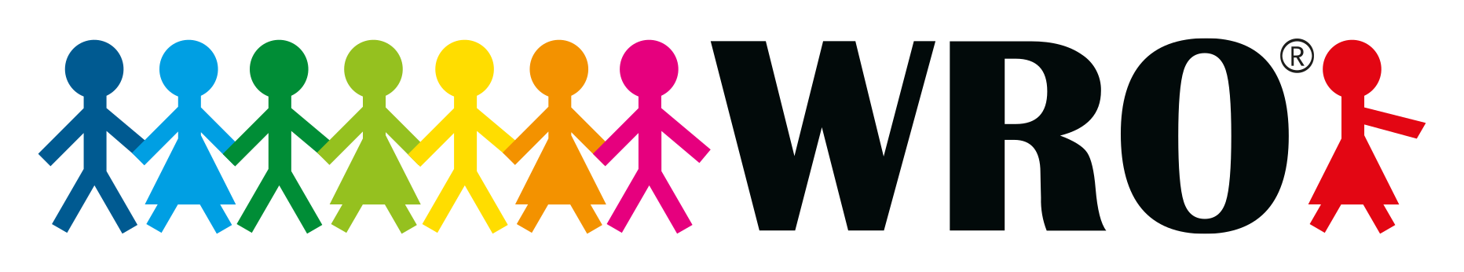
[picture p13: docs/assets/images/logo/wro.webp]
World Robot Olympiad's Logo
		
		<br>
		<i>World Robot Olympiad's Logo</i>
	</p>
	<br>
	<p align="center">
		MINCYT's Logo
		<br>
		<i>MINCYT's Logo</i>
	</p>
</div>
<!-- github-only-end -->

<!-- mkdocs-only-start
<div class="image-horizontal-container">
    <div class="hcenter">
        <img src="/assets/images/logo/wro.webp" alt="World Robot Olympiad's Logo" 
    class="logo--education">
        <i>World Robot Olympiad's Logo</i>
    </div>
    <div class="hcenter">
        <img src="/assets/images/logo/mincyt.png" alt="MINCYT's Logo" 
    class="logo--education">
        <i>MINCYT's Logo</i>
    </div>
</div>
mkdocs-only-end -->

Below is an index with all the links to access all the different sections of this documentation. Each section has detailed information about the robot's technical aspects, including the mechanics, source code, the different devices, the components, the schemes and diagrams, the team's photos and videos of Klevor in action. Also, we included additional resources to amplify the information to facilitate the comprehension for all the concepts involved.

<!-- github-only-start -->
<p align="center">
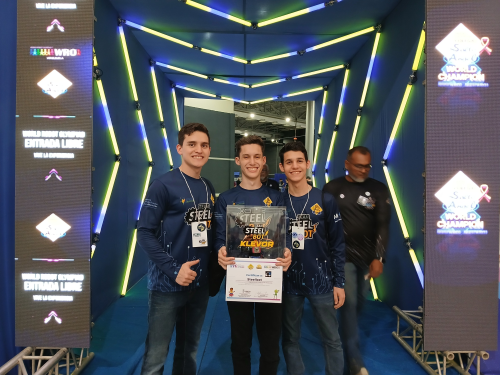
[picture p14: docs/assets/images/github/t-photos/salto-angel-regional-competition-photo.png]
Team Steel Bot at Salto Ángel's regional competition
	
	<br>
	<i>Team Steel Bot at Salto Ángel's regional competition</i>
</p>
<!-- github-only-end -->

<!-- mkdocs-only-start
<div class="hcenter">
    <img src="/assets/images/github/t-photos/salto-angel-regional-competition-photo.png" alt="Team Steel Bot at Salto Ángel's regional competition" 
class="picture--team">
    <i>Team Steel Bot at Salto Ángel's regional competition</i>
</div>
mkdocs-only-end -->

## Index

1. **[About us](about.en.md)**
2. **Electronics**
	1. Components
		1. [Previous Components](electronic/components/previous.en.md)
		2. [Current Components](electronic/components/current.en.md)
		3. [Future Components](electronic/components/future.en.md)
	2. Diagrams
		1. [Connection Diagrams](electronic/diagrams/wiring.en.md)
3. **Mechanics**
	1. Parts
		1. Common Parts
			1. [Previous Common Parts](mechanical/parts/common/previous.en.md)
			2. [Present Common Parts](mechanical/parts/common/current.en.md)
		2. [Prototype 1's Parts](mechanical/parts/prototype1.en.md)
		3. [Prototype 2's Parts](mechanical/parts/prototype2.en.md)
		4. [Prototype 3's Parts](mechanical/parts/prototype3.en.md)
       	5. [Prototype 4's Parts](mechanical/parts/prototype4.en.md)
	2. Prototypes
		1. [Prototype 1](mechanical/prototypes/prototype1.en.md)
		2. [Prototype 2](mechanical/prototypes/prototype2.en.md)
		3. [Prototype 3](mechanical/prototypes/prototype3.en.md)
		4. [Prototype 4](mechanical/prototypes/prototype4.en.md)
4. **Programming**
	1. Programming Languages
		1. [Previous Programming Languages](programming/languages/previous.en.md)
		2. [Current Programming Languages](programming/languages/current.en.md)
		3. [Future Programming Languages](programming/languages/future.en.md)
	2. Libraries
		1. Legacy
			1. [CircuitPython Libraries](programming/libraries/legacy/circuit-python.en.md)
		2. [Python Libraries](programming/libraries/python.en.md)
	3. Diagrams
		1. [Flowchart](programming/diagrams/flowcharts.en.md)
	4. [Glossary](programming/glossary.en.md)
	5. Guides
   		1. Legacy
			1. [CircuitPython's Guide](programming/guides/legacy/circuit-python.en.md)
            2. [MicroPython's Guide](programming/guides/legacy/micro-python.en.md)
            3. [Raspberry Pi Pico 2 W's Guide](programming/guides/legacy/raspberry-pi-pico-2w.en.md)
		2. [MkDocs' Guide](programming/guides/mkdocs.en.md)
    	3. [TinyGo's Guide](programming/guides/tinygo.en.md)
		4. [Raspberry Pi 5's  Guide](programming/guides/raspberry-pi-5.en.md)
		5. [Raspberry Pi Pico 2 W's Guide](programming/guides/raspberry-pi-pico-2w.en.md)
		6. [Object Detection's Guide](programming/guides/object-detection.en.md)
5. **[GitHub](github.en.md)**
6. **[Videos](videos.en.md)**
7. **[Software](software.en.md)**
8. **[Gadgets](gadgets.en.md)**
9. **[Sponsors](sponsors.en.md)**
10. **[Contact Us](contact.en.md)**

## Sponsors

<!-- github-only-start -->
<p align="center">
	<a href="sponsors.en.md#viajes-giorgio">
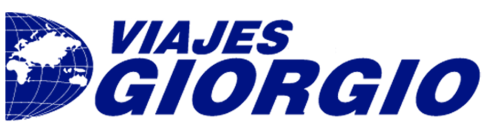
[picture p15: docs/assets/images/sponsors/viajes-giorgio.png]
Viajes Giorgio's Logo
		
		<br>
		<i>Viajes Giorgio's Logo</i>
	</a>
	<br>
	<a href="sponsors.en.md#nathalys-star">
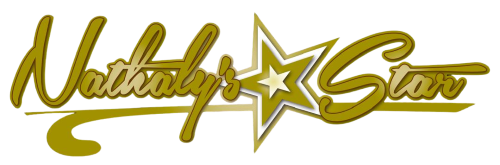
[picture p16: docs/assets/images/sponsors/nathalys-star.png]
Nathaly's Star's Logo
		
		<br>
		<i>Nathaly's Star's Logo</i>
	</a>
	<br>
	<a href="sponsors.en.md#steel-ca">
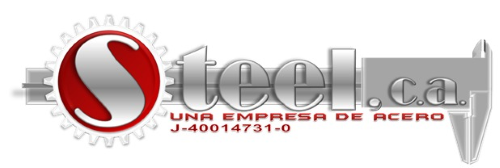
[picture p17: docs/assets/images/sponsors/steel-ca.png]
Steel C.A.'s Logo
		
		<br>
		<i>Steel C.A.'s Logo</i>
	</a>
</p>
<!-- github-only-end -->

<!-- mkdocs-only-start
<div class="hcenter">
    <a href="sponsors.html#viajes-giorgio">
        <img src="/assets/images/sponsors/viajes-giorgio.png" alt="Viajes Giorgio's Logo" 
class="logo--sponsor">
    </a>
    <i>Viajes Giorgio's Logo</i>
</div>

<div class="hcenter">
    <a href="sponsors.html#nathalys-star">
        <img src="/assets/images/sponsors/nathalys-star.png" alt="Nathaly's Star's Logo" 
class="logo--sponsor">
    </a>
    <i>Nathaly's Star's Logo</i>
</div>

<div class="hcenter">
    <a href="sponsors.html#steel-ca">
        <img src="/assets/images/sponsors/steel-ca.png" alt="Steel C.A.'s Logo" 
class="logo--sponsor">
    </a>
    <i>Steel C.A.'s Logo</i>
</div>
mkdocs-only-end -->

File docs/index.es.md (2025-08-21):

# Inicio

<!-- github-only-start -->
<p align="center">
	Logo del Equipo Steel Bot
	<br>
	<i>Logo del Equipo Steel Bot</i>
</p>
<!-- github-only-end -->

<!-- mkdocs-only-start
<div class="hcenter">
    <img src="/assets/images/logo/teamsteelbot.png" alt="Logo del Equipo Steel Bot" 
class="logo--team">
    <i>Logo del Equipo Steel Bot</i>
</div>
mkdocs-only-end -->

Bienvenidos a la documentación de Klevor, un robot autónomo diseñado para participar en la competencia de robótica de la World Robot Olympiad 2025, en la categoría Futuros Ingenieros. Esta documentación contiene toda la información necesaria para entender su funcionamiento, los dispositivos utilizados, el código implementado, los componentes y más. Esperamos que la misma sea útil tanto para los jueces como para cualquier persona interesada en aprender sobre este proyecto.

<!-- github-only-start -->
<div>
	<p align="center">
		Logo de la World Robot Olympiad
		<br>
		<i>Logo de la World Robot Olympiad</i>
	</p>
	<br>	
	<p align="center">
		Logo del MINCYT
		<br>
		<i>Logo del MINCYT</i>
	</p>
</div>
<!-- github-only-end -->

<!-- mkdocs-only-start
<div class="image-horizontal-container">
    <div class="hcenter">
        <img src="/assets/images/logo/wro.webp" alt="Logo de la World Robot Olympiad" 
    class="logo--education">
        <i>Logo de la World Robot Olympiad</i>
    </div>
    <div class="hcenter">
        <img src="/assets/images/logo/mincyt.png" alt="Logo del MINCYT" 
    class="logo--education">
        <i>Logo del MINCYT</i>
    </div>
</div>
mkdocs-only-end -->

A continuación se presenta un índice con los enlaces a las diferentes secciones de la documentación. Cada sección contiene información detallada sobre los aspectos técnicos y prácticos del robot, incluyendo la mecánica, el código, los dispositivos utilizados, los componentes, los esquemas y diagramas, las fotos del equipo y los vídeos de Klevor en acción. Además, se incluyen recursos externos para ampliar la información y facilitar la comprensión de los conceptos presentados.

<!-- github-only-start -->
<p align="center">
	Equipo Steel Bot en la competencia regional del Salto Ángel
	<br>
	<i>Equipo Steel Bot en la competencia regional del Salto Ángel</i>
</p>
<!-- github-only-end -->

<!-- mkdocs-only-start
<div class="hcenter">
    <img src="/assets/images/github/t-photos/salto-angel-regional-competition-photo.png" alt="Equipo Steel Bot en la competencia regional del Salto Ángel" 
class="picture--team">
    <i>Equipo Steel Bot en la competencia regional del Salto Ángel</i>
</div>
mkdocs-only-end -->

## Índice

1. **[Sobre Nosotros](about.es.md)**
2. **Electrónica**
	1. Componentes
		1. [Componentes Previos](electronic/components/previous.es.md)
		2. [Componentes Actuales](electronic/components/current.es.md)
		3. [Componentes Futuros](electronic/components/future.es.md)
	2. Diagramas
		1. [Diagramas de Conexiones](electronic/diagrams/wiring.es.md)
3. **Mecánica**
	1. Piezas
		1. Piezas Comunes
			1. [Piezas Comunes Previas](mechanical/parts/common/previous.es.md)
			2. [Piezas Comunes Actuales](mechanical/parts/common/current.es.md)
		2. [Piezas del Prototipo 1](mechanical/parts/prototype1.es.md)
		3. [Piezas del Prototipo 2](mechanical/parts/prototype2.es.md)
		4. [Piezas del Prototipo 3](mechanical/parts/prototype3.es.md)
       	5. [Piezas del Prototipo 4](mechanical/parts/prototype4.es.md)
	2. Prototipos
		1. [Prototipo 1](mechanical/prototypes/prototype1.es.md)
		2. [Prototipo 2](mechanical/prototypes/prototype2.es.md)
		3. [Prototipo 3](mechanical/prototypes/prototype3.es.md)
		4. [Prototipo 4](mechanical/prototypes/prototype4.es.md)
4. **Programación**
	1. Lenguajes de Programación
        1. [Lenguajes de Programación Previos](programming/languages/previous.es.md)
        2. [Lenguajes de Programación Actuales](programming/languages/current.es.md)
        3. [Lenguajes de Programación Futuros](programming/languages/future.es.md)
	2. Librerías
   		1. Legado:
           1. [Librerías de CircuitPython](programming/libraries/legacy/circuit-python.es.md)
		2. [Librerías de Python](programming/libraries/python.es.md)
	3. Diagramas
		1. [Diagramas de Flujo](programming/diagrams/flowcharts.es.md)
	4. [Glosario de Términos](programming/glossary.es.md)
	5. Guías
   		1. Legado 
            1. [Guía de MicroPython](programming/guides/legacy/micro-python.es.md)
            2. [Guía de CircuitPython](programming/guides/legacy/circuit-python.es.md)
            3. [Guía de la Raspberry Pi Pico 2 W](programming/guides/legacy/raspberry-pi-pico-2w.es.md)
		2. [Guía de MkDocs](programming/guides/mkdocs.es.md)
       	3. [Guía de TinyGo](programming/guides/tinygo.es.md)
		4. [Guía de la Raspberry Pi 5](programming/guides/raspberry-pi-5.es.md)
		5. [Guía de la Raspberry Pi Pico 2 W](programming/guides/raspberry-pi-pico-2w.es.md)
		6. [Guía de Detección de Objetos](programming/guides/object-detection.es.md)
5. **[GitHub](github.es.md)**
6. **[Vídeos](videos.es.md)**
7. **[Software](software.es.md)**
8. **[Gadgets](gadgets.es.md)**
9. **[Patrocinadores](sponsors.es.md)**
10. **[Contacto](contact.es.md)**

## Patrocinadores

<!-- github-only-start -->
<p align="center">
	<a href="sponsors.en.md#viajes-giorgio">
		Logo de Viajes Giorgio
		<br>
		<i>Logo de Viajes Giorgio</i>
	</a>
	<br>
	<a href="sponsors.en.md#nathalys-star">
		Logo de Nathaly's Star
		<br>
		<i>Logo de Nathaly's Star</i>
	</a>
	<br>
	<a href="sponsors.en.md#steel-ca">
		Logo de Steel C.A.
		<br>
		<i>Logo de Steel C.A.</i>
	</a>
</p>
<!-- github-only-end -->

<!-- mkdocs-only-start
<div class="hcenter">
    <a href="sponsors.html#viajes-giorgio">
        <img src="/assets/images/sponsors/viajes-giorgio.png" alt="Logo de Viajes Giorgio" 
class="logo--sponsor">
    </a>
    <i>Logo de Viajes Giorgio</i>
</div>

<div class="hcenter">
    <a href="sponsors.html#nathalys-star">
        <img src="/assets/images/sponsors/nathalys-star.png" alt="Logo de Nathaly's Star" 
class="logo--sponsor">
    </a>
    <i>Logo de Nathaly's Star</i>
</div>

<div class="hcenter">
    <a href="sponsors.html#steel-ca">
        <img src="/assets/images/sponsors/steel-ca.png" alt="Logo de Steel C.A." 
class="logo--sponsor">
    </a>
    <i>Logo de Steel C.A.</i>
</div>
mkdocs-only-end -->

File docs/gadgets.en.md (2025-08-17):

# Gadgets

## Digital Multimeter with USB-C Port 4-30 V 0-12 A

<!-- github-only-start -->
<p align="center">
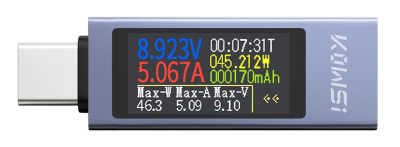
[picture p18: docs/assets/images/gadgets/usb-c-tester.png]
Digital Multimeter with USB-C Port 4-30 V 0-12 A
	
	<br>
	<i>Digital Multimeter with USB-C Port 4-30 V 0-12 A</i>
</p>
<!-- github-only-end -->

<!-- mkdocs-only-start
<div class="hcenter">
    <img src="/assets/images/gadgets/usb-c-tester.png" alt="Digital Multimeter with USB-C Port 4-30 V 0-12 A" 
class="gadget-image">
    <i>Digital Multimeter with USB-C Port 4-30 V 0-12 A</i>
</div>
mkdocs-only-end -->

This Digital Multimeter with a USB-C Port is a very versatile tool that is capable of measuring both the voltage and the amperage for multiple devices that implement this type of connection. It's pretty useful to check our battery's state, the charging efficiency and overall health of our electronics.

In our case, this was especially useful whenever we wanted to check that our Raspberry Pi 5 was receiving the correct amperage through the USB-C port, assuring an optimal device performance. Also, its capacity to measure voltage and amperage in real-time facilitates the diagnosis for any electronics issue within any of our projects..

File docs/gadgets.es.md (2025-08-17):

# Gadgets

## Multímetro Digital con Puerto USB-C 4-30 V 0-12 A 

<!-- github-only-start -->
<p align="center">
	Multímetro Digital con Puerto USB-C 4-30 V 0-12 A
	<br>
	<i>Multímetro Digital con Puerto USB-C 4-30 V 0-12 A</i>
</p>
<!-- github-only-end -->

<!-- mkdocs-only-start
<div class="hcenter">
    <img src="/assets/images/gadgets/usb-c-tester.png" alt="Multímetro Digital con Puerto USB-C 4-30 V 0-12 A" 
class="gadget-image">
    <i>Multímetro Digital con Puerto USB-C 4-30 V 0-12 A</i>
</div>
mkdocs-only-end -->

El multímetro digital con puerto USB-C es una herramienta versátil que permite medir voltaje y corriente en dispositivos que utilizan este tipo de conexión. Es especialmente útil para verificar el estado de carga de baterías, la eficiencia de cargadores y la salud general de los circuitos electrónicos.

En nuestro caso, fue de gran utilidad para comprobar que la Raspberry Pi 5 estaba recibiendo la corriente adecuada a través del puerto USB-C, asegurando un funcionamiento óptimo del dispositivo. Además, su capacidad para medir voltajes y corrientes en tiempo real facilita el diagnóstico de problemas eléctricos en proyectos de electrónica.

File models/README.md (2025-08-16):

# Modelos

Esta carpeta contiene todos los modelos, planos y vistas correspondientes al desarrollo de Klevor.

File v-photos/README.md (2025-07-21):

# Fotos del Vehículo

Esta carpeta contiene todas las imágenes correspondientes al desarrollo de
Klevor.

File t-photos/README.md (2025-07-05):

# Fotos del Equipo

Esta carpeta contiene todas las fotos del equipo de Steel Bot.

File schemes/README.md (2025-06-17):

# Diagramas

Esta carpeta contiene todos los diagramas correspondientes al desarrollo de Klevor.

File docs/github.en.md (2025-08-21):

# GitHub

## Repository

<!-- github-only-start -->
<p align="center">
	GitHub's Logo
	<br>
	<i>GitHub's Logo</i>
</p>
<!-- github-only-end -->

<!-- mkdocs-only-start
<div class="hcenter">
    <img src="/assets/images/logo/github.png" alt="GitHub's Logo" 
class="logo--3rd-party">
    <i>GitHub's Logo</i>
</div>
mkdocs-only-end -->

This project can be found in GitHub, where you can find the source code, documentation, 3D models, diagrams and flowcharts from our robot, Klevor. This repository is organized within multiple folders and files, every one of them containing specific information about our robot and its development. You can access the repository through the following link: [https://github.com/teamsteelbot/klevor](https://github.com/teamsteelbot/klevor)

Also, you can download it directly through the terminal using the following command:

```bash
git clone https://github.com/teamsteelbot/klevor.git
```

> [!IMPORTANT]
> To clone the submodules too, you can use the following command:
>
> ```bash
> git clone --recurse-submodules https://github.com/teamsteelbot/klevor.git
> ```

<!-- github-only-start -->
<p align="center">
	Git's Logo
	<br>
	<i>Git's Logo</i>
</p>
<!-- github-only-end -->

<!-- mkdocs-only-start
<div class="hcenter">
    <img src="/assets/images/logo/git.png" alt="Git's Logo" 
class="logo--3rd-party">
    <i>Git's Logo</i>
</div>
mkdocs-only-end -->

> [!NOTE]
> To be able to clone our repository, it is mandatory to have Git installed on your computer. You can download Git [here](https://git-scm.com/downloads).

## Repository Structure

- **devices**: contains all the source code that was used to control this robot autonomously.

- **docs**: contains all the documentation related to Klevor, including information about the components, the diagrams, photos and videos.

- **models**: contains all the 3D files that were used to be able to build Klevor.

- **schemes**: contains all the schemes and the connection diagrams from Klevor.

- **t-photos**: contains the team's photos.

- **v-photos**: contains the Klevor's photos

- **video**: contains the videos where Klevor is on the game field, solving both the Open Challenge and Closed Challenge.

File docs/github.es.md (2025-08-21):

# GitHub

## Repositorio

<!-- github-only-start -->
<p align="center">
	Logo de GitHub
	<br>
	<i>Logo de GitHub</i>
</p>
<!-- github-only-end -->

<!-- mkdocs-only-start
<div class="hcenter">
    <img src="/assets/images/logo/github.png" alt="Logo de GitHub" 
class="logo--3rd-party">
    <i>Logo de GitHub</i>
</div>
mkdocs-only-end -->

El presente proyecto puede ser encontrado en GitHub, donde se encuentra todo el código, documentación, modelos 3D y esquemas de Klevor, nuestro robot. El repositorio está organizado en varias carpetas y archivos, cada uno de los cuales contiene información específica sobre el robot y su desarrollo. Puedes acceder al repositorio a través del siguiente enlace: [https://github.com/teamsteelbot/klevor](https://github.com/teamsteelbot/klevor)

También, puedes descargarlo directamente desde la terminal utilizando el siguiente comando:

```bash
git clone https://github.com/teamsteelbot/klevor.git
```

> [!IMPORTANT]
> Para clonar también los submódulos, puedes utilizar el siguiente comando:
>
> ```bash
> git clone --recurse-submodules https://github.com/teamsteelbot/klevor.git
> ```

<!-- github-only-start -->
<p align="center">
	Logo de Git
	<br>
	<i>Logo de Git</i>
</p>
<!-- github-only-end -->

<!-- mkdocs-only-start
<div class="hcenter">
    <img src="/assets/images/logo/git.png" alt="Logo de Git" 
class="logo--3rd-party">
    <i>Logo de Git</i>
</div>
mkdocs-only-end -->

> [!NOTE]
> Para poder clonar el repositorio, es necesario tener instalado Git en tu computadora. Puedes descargarlo desde [aquí](https://git-scm.com/downloads).

## Estructura del Repositorio

- **devices**: contiene todo el código el cual fue utilizado para poder controlar este robot de manera autónoma.

- **docs**: contiene toda la documentación de este robot, incluyendo información sobre los componentes, diagramas, fotos y vídeos.

- **models**: contiene todos los archivos en 3D que se utilizaron para poder construir a nuestro robot.

- **schemes**: contiene todos los esquemas y diagramas de todas las conexiones de nuestro robot.

- **t-photos**: contiene las fotos del equipo.

- **v-photos**: contiene las fotos de Klevor.

- **video**: contiene los vídeos de Klevor en la pista, tanto en el Desafío sin Obstáculos como en el Desafío con Obstáculos.

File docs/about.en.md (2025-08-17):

# About Us

<!-- github-only-start -->
<p align="center">
	Team Steel Bot's Logo
	<br>
	<i>Team Steel Bot's Logo</i>
</p>
<!-- github-only-end -->

<!-- mkdocs-only-start
<div class="hcenter">
    <img src="/assets/images/logo/teamsteelbot.png" alt="Team Steel Bot's Logo" 
class="logo--team">
    <i>Team Steel Bot's Logo</i>
</div>
mkdocs-only-end -->

This is Team Steel Bot's repository, or well, the documentation, a participating team in the World Robot Olympiad 2025, in the Future Engineers category. Representing the Salto Angel School, in Maracaibo, Estado Zulia, Venezuela.

<!-- github-only-start -->
<p align="center">
	World Robot Olympiad's Logo
	<br>
	<i>World Robot Olympiad's Logo</i>
</p>
<!-- github-only-end -->

<!-- mkdocs-only-start
<div class="hcenter">
	<img src="/assets/images/logo/wro.webp" alt="World Robot Olympiad's Logo" 
class="logo--education">
	<i>World Robot Olympiad's Logo</i>
</div>
mkdocs-only-end -->

Currently, this team is conformed by 3 members:

- **Ramón Álvarez**, 19 years old. [ralvarezdev](https://github.com/ralvarezdev). The team's captain and in charge of the robot's code. Currently, he is in his 9th trimester in Computer Engineering at Universidad Rafael Urdaneta (URU).
- **Sebastián Álvarez**, 15 years old. [salvarezdev](https://github.com/salvarezdev). Currently in charge of robot's code, the documentation and the robot's logic. Currently, he is in his 4th year of high school at Colegio Salto Ángel.
- **Otto Piñero**, 16 years old. [Ottorafaelpg](https://github.com/Ottorafaelpg). Currently, in charge of the robot's design and manufacturing, he is also in his 4th year of high school at Colegio Salto Ángel.

<!-- github-only-start -->
<p align="center">
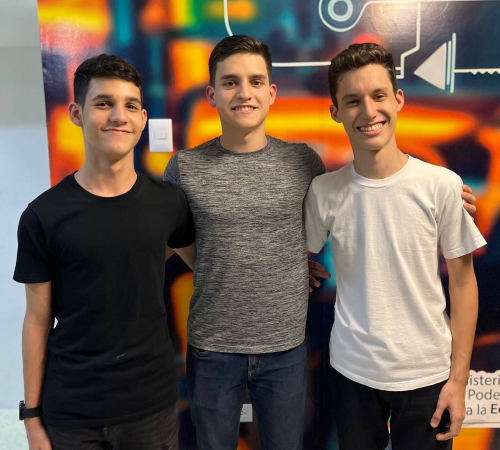
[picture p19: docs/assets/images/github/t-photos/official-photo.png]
From left to right: Sebastián Álvarez, Ramón Álvarez and Otto Piñero
	
	<br>
	<i>From left to right: Sebastián Álvarez, Ramón Álvarez and Otto Piñero</i>
</p>

<div>
	<p align="center">
		Universidad Rafael Urdaneta's Logo
		<br>
		<i>Universidad Rafael Urdaneta's Logo</i>
	</p>
	<p align="center">
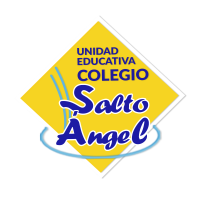
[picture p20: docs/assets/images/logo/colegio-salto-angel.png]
Colegio Salto Ángel's Logo
		
		<br>
		<i>Colegio Salto Ángel's Logo</i>
	</p>
</div>
<!-- github-only-end -->

<!-- mkdocs-only-start
<div class="hcenter">
    <img src="/assets/images/github/t-photos/official-photo.png" alt="From left to right: Sebastián Álvarez, Ramón Álvarez and Otto Piñero" 
class="picture--team">
    <i>From left to right: Sebastián Álvarez, Ramón Álvarez and Otto Piñero</i>
</div>

<div class="image-horizontal-container">
    <div class="hcenter">
        <img src="/assets/images/logo/uru.png" alt="Universidad Rafael Urdaneta's Logo" 
    class="logo--education">
        <i>Universidad Rafael Urdaneta's Logo</i>
    </div>
    <div class="hcenter">
        <img src="/assets/images/logo/colegio-salto-angel.png" alt="Colegio Salto Ángel's Logo" 
    class="logo--education">
        <i>Colegio Salto Ángel's Logo</i>
    </div>
</div>
mkdocs-only-end -->

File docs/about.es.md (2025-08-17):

# Sobre Nosotros

<!-- github-only-start -->
<p align="center">
	Logo del Equipo Steel Bot
	<br>
	<i>Logo del Equipo Steel Bot</i>
</p>
<!-- github-only-end -->

<!-- mkdocs-only-start
<div class="hcenter">
    <img src="/assets/images/logo/teamsteelbot.png" alt="Logo del Equipo Steel Bot" 
class="logo--team">
    <i>Logo del Equipo Steel Bot</i>
</div>
mkdocs-only-end -->

Este es el repositorio, o en su defecto la documentación, del Team Steel Bot, equipo compitiendo en la World Robot Olympiad 2025, en la categoría Futuros Ingenieros. Representando al Colegio Salto Ángel en Maracaibo, Estado Zulia, Venezuela.

<!-- github-only-start -->
<p align="center">
	Logo de la World Robot Olympiad
	<br>
	<i>Logo de la World Robot Olympiad</i>
</p>
<!-- github-only-end -->

<!-- mkdocs-only-start
<div class="hcenter">
	<img src="/assets/images/logo/wro.webp" alt="Logo de la World Robot Olympiad" 
class="logo--education">
	<i>Logo de la World Robot Olympiad</i>
</div>
mkdocs-only-end -->

Actualmente, este equipo está conformado por 3 miembros:

- **Ramón Álvarez**, 19 años. [ralvarezdev](https://github.com/ralvarezdev). Ejerce como líder del equipo y es el encargado de la programación. Actualmente, cursa el 9no trimestre de Ingeniería en Computación en la Universidad Rafael Urdaneta (URU).
- **Sebastián Álvarez**, 15 años. [salvarezdev](https://github.com/salvarezdev). Encargado tanto de la programación, como de la documentación y la toma de decisiones con respecto a la lógica del robot. Actualmente, cursa el 4to año de bachillerato en el Colegio Salto Ángel.
- **Otto Piñero**, 16 años. [Ottorafaelpg](https://github.com/Ottorafaelpg). Encargado del diseño y la fabricación del robot. Actualmente, cursa el 4to año de bachillerato en el Colegio Salto Ángel.

<!-- github-only-start -->
<p align="center">
	De izquierda a derecha: Sebastián Álvarez, Ramón Álvarez y Otto Piñero
	<br>
	<i>De izquierda a derecha: Sebastián Álvarez, Ramón Álvarez y Otto Piñero</i>
</p>

<div>
	<p align="center">
		Logo de la Universidad Rafael Urdaneta
		<br>
		<i>Logo de la Universidad Rafael Urdaneta</i>
	</p>
	<p align="center">
		Logo del Colegio Salto Ángel
		<br>
		<i>Logo del Colegio Salto Ángel</i>
	</p>
</div>
<!-- github-only-end -->

<!-- mkdocs-only-start
<div class="hcenter">
    <img src="/assets/images/github/t-photos/official-photo.png" alt="De izquierda a derecha: Sebastián Álvarez, Ramón Álvarez y Otto Piñer" 
class="picture--team">
    <i>De izquierda a derecha: Sebastián Álvarez, Ramón Álvarez y Otto Piñero</i>
</div>

<div class="image-horizontal-container">
    <div class="hcenter">
        <img src="/assets/images/logo/uru.png" alt="Logo de la Universidad Rafael Urdaneta" 
    class="logo--education">
        <i>Logo de la Universidad Rafael Urdaneta</i>
    </div>
    <div class="hcenter">
        <img src="/assets/images/logo/colegio-salto-angel.png" alt="Logo del Colegio Salto Ángel" 
    class="logo--education">
        <i>Logo del Colegio Salto Ángel</i>
    </div>
</div>
mkdocs-only-end -->

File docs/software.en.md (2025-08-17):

# Software

Here you can find all the different programs that we used as Team Steel bot to be able to develop Klevor.

## Programming

### Label Studio

<!-- github-only-start -->
<p align="center">
	Label Studio's Logo
	<br>
	<i>Label Studio's Logo</i>
</p>
<!-- github-only-end -->

<!-- mkdocs-only-start
<div class="hcenter">
    <img src="/assets/images/logo/label-studio.png" alt="Label Studio's Logo" 
class="logo--3rd-party">
    <i>Label Studio's Logo</i>
</div>
mkdocs-only-end -->

[Label Studio](https://labelstud.io/) is an open-source program that helped us prepare the photos to be able to train Artificial Intelligence for the Object Detection. However, this program is not limited to this, you are able to assign tags to a wide variety of media, such as text, audio, images, videos, time series, multi-domain among many others.

In Klevor's case, this program was used to [highlight](programming/guides/object-detection.en.md#model-creation) where are the traffic signs in the training photos, then after training the AI model (you can do it locally or in the cloud) the model can recognize the traffic signs by itself.

### Google Colab

<!-- github-only-start -->
<p align="center">
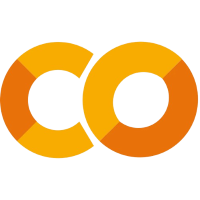
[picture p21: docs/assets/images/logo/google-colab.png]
Google Colab's Logo
	
	<br>
	<i>Google Colab's Logo</i>
</p>
<!-- github-only-end -->

<!-- mkdocs-only-start
<div class="hcenter">
    <img src="/assets/images/logo/google-colab.png" alt="Google Colab's Logo" 
class="logo--3rd-party">
    <i>Google Colab's Logo</i>
</div>
mkdocs-only-end -->

As we mentioned before, an AI model has to be trained, either locally or in the cloud, Google Colab fulfills this exact functions. [Google Colab](https://colab.research.google.com/) is a service that allows you to execute Python code onto your own web browser, also providing free access to GPUs and TPUs that can be used online, and you can link your own Google Drive to store the files generated by the model's training.

We used this platform to [train the YOLO Model](programming/guides/object-detection.en.md#model-training) mentioned before, through the use of a GPU, the Nvidia A100, which is one of the most powerful GPUs available, thanks to it, we were able to train the AI model in a relatively short time for a very low price.

### Visual Studio Code

<!-- github-only-start -->
<p align="center">
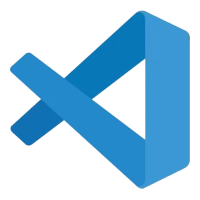
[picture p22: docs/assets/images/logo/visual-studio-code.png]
Visual Studio Code's Logo
	
	<br>
	<i>Visual Studio Code's Logo</i>
</p>
<!-- github-only-end -->

<!-- mkdocs-only-start
<div class="hcenter">
    <img src="/assets/images/logo/visual-studio-code.png" alt="Visual Studio Code's Logo" 
class="logo--3rd-party">
    <i>Visual Studio Code's Logo</i>
</div>
mkdocs-only-end -->

[Visual Studio Code](https://code.visualstudio.com/) is a software development program, with an integrated terminal, native Git support, and also supports almost every programming language, countless extensiones, and it is also fully customizable.

We used Visual Studio Code mainly on the Raspberry Pi 5, and in the lower-end team's computers, because this program is lighter than many other software development programs, like PyCharm, and it also allows the user to work with multiple programming languages, which is crucial for Klevor's development.

### PyCharm 

<!-- github-only-start -->
<p align="center">
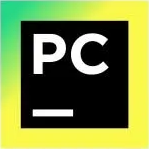
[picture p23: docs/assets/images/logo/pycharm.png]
PyCharm's Logo
	
	<br>
	<i>PyCharm's Logo</i>
</p>
<!-- github-only-end -->

<!-- mkdocs-only-start
<div class="hcenter">
    <img src="/assets/images/logo/pycharm.png" alt="PyCharm's Logo" 
class="logo--3rd-party">
    <i>PyCharm's Logo</i>
</div>
mkdocs-only-end -->

[PyCharm](https://www.jetbrains.com/pycharm/) is another software development program; however, this program has a lot more functionality than Visual Studio Code, however, there is a small little detail, PyCharm requires a license to use the Pro version, meanwhile Visual Studio Code doesn't need a license. Also, PyCharm is specifically an Integrated Development Environment (IDE) for Python, meanwhile Visual Studio Code is a more general code editor, which is why PyCharm offers more advanced characteristics, meant to be used exclusively for Python, such as the advanced debugging, the code refactoring, database integration, among many others.

We used PyCharm to check and debug Klevor's source code with ease, because this program has a lot more advanced debugging tools and code analysis, which help us spot any bugs and fix them in the most efficient way possible.

### Thonny

<!-- github-only-start -->
<p align="center">
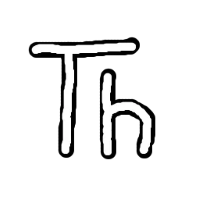
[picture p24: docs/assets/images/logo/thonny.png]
Thonny's Logo
	
	<br>
	<i>Thonny's Logo</i>
</p>
<!-- github-only-end -->

<!-- mkdocs-only-start
<div class="hcenter">
    <img src="/assets/images/logo/thonny.png" alt="Thonny's Logo" 
class="logo--3rd-party">
    <i>Thonny's Logo</i>
</div>
mkdocs-only-end -->

[Thonny](https://thonny.org/) is another software development program, used mainly to execute code Python code directly onto microcontrollers, in our case, it waw the Raspberry Pi Pico 2 W, either to test code, or using it on the field. It is worth mentioning that, unlike the other software development programs mentioned before, Thonny is an IDE designed specifically for beginners in Python, which makes it easier to use and understand for those who are starting to learn the language. Also, Thonny has a much simpler and less overwhelming than PyCharm or Visual Studio Code, and also it integrates direct functionalities to work with microcontrollers, like the Raspberry Pi Pico 2 W.

## Design 

### Canva

<!-- github-only-start -->
<p align="center">
	Canva's Logo
	<br>
	<i>Canva's Logo</i>
</p>
<!-- github-only-end -->

<!-- mkdocs-only-start
<div class="hcenter">
    <img src="/assets/images/logo/canva.png" alt="Canva's Logo" 
class="logo--3rd-party">
    <i>Canva's Logo</i>
</div>
mkdocs-only-end -->

[Canva](https://www.canva.com/) is an online design platform, which allows any user to design practically anything in 2D, we decided to use Canva mainly to design the connection diagrams and the flowcharts, as a quick and effective solution for our documentation, however as we started to design them, we realized that these diagrams were too complex and took way too long to make, so we decided to switch to other online alternatives.

### Mermaid

<!-- github-only-start -->
<p align="center">
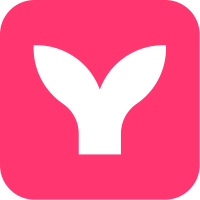
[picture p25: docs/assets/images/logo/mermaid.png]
Mermaid's Logo
	
	<br>
	<i>Mermaid's Logo</i>
</p>
<!-- github-only-end -->

<!-- mkdocs-only-start
<div class="hcenter">
    <img src="/assets/images/logo/mermaid.png" alt="Mermaid's Logo" 
class="logo--3rd-party">
    <i>Mermaid's Logo</i>
</div>
mkdocs-only-end -->

After not getting the results we expected with Canva, we decided to switch to [Mermaid](https://www.mermaidchart.com/), which an open-source program that specializes in creating diagrams with text, with a similar syntax to Markdown, to design our diagrams and flowcharts.

### Draw.io

<!-- github-only-start -->
<p align="center">
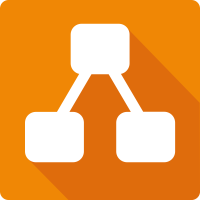
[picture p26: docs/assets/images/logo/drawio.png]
Draw.io's Logo
	
	<br>
	<i>Draw.io's Logo</i>
</p>
<!-- github-only-end -->

<!-- mkdocs-only-start
<div class="hcenter">
    <img src="/assets/images/logo/drawio.png" alt="Draw.io's Logo" 
class="logo--3rd-party">
    <i>Draw.io's Logo</i>
</div>
mkdocs-only-end -->

[Draw.io](https://www.drawio.com/) is a web browser that allows the online creation of diagrams, with the added feature that multiple users can modify the same diagram at the same time, with a similar interface to Microsoft Visio, with the advantage that Draw.io is completely free and open-source. We decided to use Draw.io for the designing of diagrams and flowcharts, because this program allowed us to create more complex and more detailed diagrams, while also being easier to use than Canva.

### Fusion 360

<!-- github-only-start -->
<p align="center">
	Fusion 360's Logo
	<br>
	<i>Fusion 360's Logo</i>
</p>
<!-- github-only-end -->

<!-- mkdocs-only-start
<div class="hcenter">
    <img src="/assets/images/logo/fusion-360.png" alt="Fusion 360's Logo" 
class="logo--3rd-party">
    <i>Fusion 360's Logo</i>
</div>
mkdocs-only-end -->

[Fusion 360](https://www.autodesk.com/products/fusion-360/overview) is a 3D design program, made by Autodesk, with this program, we were able to design the pieces we needed and export them to `.stl` format, with which we were able to 3D print them. It is also a very versatile program for draftsmen, engineers, manufacturers and the creation of equipment, since it has a lot of functions, like rendering, design, component weighing, PCB designing, simulations, free-form modeling, etc.

We decided to use this program because it's pretty much an "all-in-one" solution which combines computer-assisted design, manufacturing, engineering and the PCB design, which turns it into a pretty comfortable solution.

## Planning

### Jira

<!-- github-only-start -->
<p align="center">
	Jira's Logo
	<br>
	<i>Jira's Logo</i>
</p>
<!-- github-only-end -->

<!-- mkdocs-only-start
<div class="hcenter">
    <img src="/assets/images/logo/jira.png" alt="Jira's Logo" 
class="logo--3rd-party">
    <i>Jira's Logo</i>
</div>
mkdocs-only-end -->

[Jira](https://www.atlassian.com/software/jira) is a web browser whose objective is to organize a team's tasks as assign them a priority, basically it is a work organization page.

In our case, using Jira allowed us to keep Klevor's development at a constant rate, because each member had a different tasks and a certain time to complete it, which made us able to advance in a much more efficent and organized way.

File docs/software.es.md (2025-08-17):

# Software

Aquí se encuentran todos los programas que utilizamos como Team Steel Bot para poder desarrollar a Klevor.

## Programación

### Label Studio 

<!-- github-only-start -->
<p align="center">
	Logo de Label Studio
	<br>
	<i>Logo de Label Studio</i>
</p>
<!-- github-only-end -->

<!-- mkdocs-only-start
<div class="hcenter">
    <img src="/assets/images/logo/label-studio.png" alt="Logo de Label Studio" 
class="logo--3rd-party">
    <i>Logo de Label Studio</i>
</div>
mkdocs-only-end -->

[Label Studio](https://labelstud.io/) es un programa open-source (de código abierto) el cual nos permite preparar las fotos para poder entrenar una Inteligencia Artificial para la detección de objetos. Este programa no se limita a esta funcionalidad, ya que además permite asignar etiquetas a una gran variedad de tipos, como texto, audio, imágenes, vídeos, series de tiempo, multi-dominio, entre otros.

En el caso de Klevor, este programa se utilizó para [remarcar](programming/guides/object-detection.es.md#creación-del-modelo) dónde están los bloques en las fotos de entrenamiento para que así, después de dejar el modelo entrenando un rato (ya sea de manera local o en la nube), este pueda reconocer los bloques por sí solo.

### Google Colab

<!-- github-only-start -->
<p align="center">
	Logo de Google Colab
	<br>
	<i>Logo de Google Colab</i>
</p>
<!-- github-only-end -->

<!-- mkdocs-only-start
<div class="hcenter">
    <img src="/assets/images/logo/google-colab.png" alt="Logo de Google Colab" 
class="logo--3rd-party">
    <i>Logo de Google Colab</i>
</div>
mkdocs-only-end -->

Como se mencionó anteriormente, un modelo de Inteligencia Artificial debe ser entrenado, ya sea de manera local o en la nube, pues Google Colab cumple exactamente está función. [Google Colab](https://colab.research.google.com/) es un servicio que te permite ejecutar código en Python en tu propio navegador web, además de brindar acceso gratuito a GPU y TPU que puedan ser utilizadas en línea, así como también la posibilidad de utilizar Google Drive para almacenar los archivos generados por el entrenamiento del modelo.

En el caso de Klevor, utilizamos esta plataforma para poder [entrenar el modelo YOLO](programming/guides/object-detection.es.md#entrenamiento-del-modelo) que se mencionó anteriormente, mediante el uso de una GPU Nvidia A100, la cual es una de las más potentes del mercado, lo que nos permitió entrenar el modelo en un tiempo relativamente corto por un costo muy bajo.

### Visual Studio Code

<!-- github-only-start -->
<p align="center">
	Logo de Visual Studio Code
	<br>
	<i>Logo de Visual Studio Code</i>
</p>
<!-- github-only-end -->

<!-- mkdocs-only-start
<div class="hcenter">
    <img src="/assets/images/logo/visual-studio-code.png" alt="Logo de Visual Studio Code" 
class="logo--3rd-party">
    <i>Logo de Visual Studio Code</i>
</div>
mkdocs-only-end -->

[Visual Studio Code](https://code.visualstudio.com/) es un programa de desarrollo de software con terminal integrado, soporte nativo de Git, soporte a casi todos los lenguajes de programación, un sinnúmero de extensiones y totalmente personalizable.

En el caso de Klevor, nosotros utilizamos Visual Studio Code principalmente en la Raspberry Pi 5, como en los computadores del equipo menos potentes, ya que este programa es más ligero que otros programas de desarrollo, como PyCharm, y permite trabajar con múltiples lenguajes de programación, lo que lo hace ideal para el desarrollo de Klevor.

### PyCharm

<!-- github-only-start -->
<p align="center">
	Logo de PyCharm
	<br>
	<i>Logo de PyCharm</i>
</p>
<!-- github-only-end -->

<!-- mkdocs-only-start
<div class="hcenter">
    <img src="/assets/images/logo/pycharm.png" alt="Logo de PyCharm" 
class="logo--3rd-party">
    <i>Logo de PyCharm</i>
</div>
mkdocs-only-end -->

[PyCharm](https://www.jetbrains.com/pycharm/) es otro programa de desarrollo de software; sin embargo, este presenta muchas más funcionalidades que Visual Studio Code, con el detalle que este programa necesita de una licencia, mientras que una Visual Studio Code no necesita de una licencia. Esto es debido a que PyCharm es un programa de desarrollo integrado (IDE) para Python, lo que significa que está diseñado específicamente para trabajar con este lenguaje de programación, mientras que Visual Studio Code es un editor de código fuente más general, por lo tanto, PyCharm ofrece características más avanzadas y específicas para Python, como la depuración avanzada, la refactorización de código, la integración con bases de datos, entre otras.

En nuestro caso, empleamos PyCharm para verificar y depurar con más profundidad el código de Klevor, ya que este programa cuenta con herramientas avanzadas de depuración y análisis de código, lo que nos permitió identificar y corregir errores en el código de manera más eficiente.

### Thonny

<!-- github-only-start -->
<p align="center">
	Logo de Thonny
	<br>
	<i>Logo de Thonny</i>
</p>
<!-- github-only-end -->

<!-- mkdocs-only-start
<div class="hcenter">
    <img src="/assets/images/logo/thonny.png" alt="Logo de Thonny" 
class="logo--3rd-party">
    <i>Logo de Thonny</i>
</div>
mkdocs-only-end -->

[Thonny](https://thonny.org/) es otro programa de desarrollo integrado, utilizado principalmente para poder ejecutar código directamente en la Raspberry Pi Pico 2 W, tanto para probar, como para utilizarlo en los Desafíos. Cabe destacar que, a diferencia de las anteriores soluciones, Thonny es un IDE diseñado específicamente para principiantes en Python, lo que lo hace más fácil de usar y entender para aquellos que están empezando a aprender el lenguaje. Además, Thonny tiene una interfaz más simple y menos abrumadora que PyCharm o Visual Studio Code, así como integra funcionalidades específicas para trabajar con microcontroladores, en nuestro caso, la Raspberry Pi Pico 2 W.

## Diseño

### Canva

<!-- github-only-start -->
<p align="center">
	Logo de Canva
	<br>
	<i>Logo de Canva</i>
</p>
<!-- github-only-end -->

<!-- mkdocs-only-start
<div class="hcenter">
    <img src="/assets/images/logo/canva.png" alt="Logo de Canva" 
class="logo--3rd-party">
    <i>Logo de Canva</i>
</div>
mkdocs-only-end -->

[Canva](https://www.canva.com/) es una plataforma de diseño en línea, la cual te permite diseñar cualquier cosa en 2D, decidimos utilizar Canva principalmente para la elaboración de los diagramas de conexiones y diagramas de flujo, como una solución rápida y efectiva para la documentación, sin embargo, notamos que nuestros diagramas eran muy complejos y tomaban mucho tiempo de hacer, por lo que cambiamos a otras soluciones en línea.

### Mermaid

<!-- github-only-start -->
<p align="center">
	Logo de Mermaid
	<br>
	<i>Logo de Mermaid</i>
</p>
<!-- github-only-end -->

<!-- mkdocs-only-start
<div class="hcenter">
    <img src="/assets/images/logo/mermaid.png" alt="Logo de Mermaid" 
class="logo--3rd-party">
    <i>Logo de Mermaid</i>
</div>
mkdocs-only-end -->

Después de no lograr los resultados esperados con Canva, decidimos optar por [Mermaid](https://www.mermaidchart.com/), el cual es un programa open-source (de código abierto) que se especializa principalmente en la creación de diagramas con texto, con un sistema parecido a Markdown, con el objetivo de elaborar los diagramas de flujo.

### Draw.io

<!-- github-only-start -->
<p align="center">
	Logo de Draw.io
	<br>
	<i>Logo de Draw.io</i>
</p>
<!-- github-only-end -->

<!-- mkdocs-only-start
<div class="hcenter">
    <img src="/assets/images/logo/drawio.png" alt="Logo de Draw.io" 
class="logo--3rd-party">
    <i>Logo de Draw.io</i>
</div>
mkdocs-only-end -->

[Draw.io](https://www.drawio.com/) es una página web que permite la creación de diagramas en línea, con la posibilidad de que varios usuarios lo puedan modificar al mismo tiempo, con una interfaz muy similar a la de Microsoft Visio, pero con la ventaja de que es completamente gratuita y open-source (de código abierto). Decidimos utilizar Draw.io para la creación de los diagramas de conexiones y esquemas eléctricos, ya que nos permitió crear diagramas más complejos y detallados, además de ser más fácil de usar que Canva.

### Fusion 360

<!-- github-only-start -->
<p align="center">
	Logo de Fusion 360
	<br>
	<i>Logo de Fusion 360</i>
</p>
<!-- github-only-end -->

<!-- mkdocs-only-start
<div class="hcenter">
    <img src="/assets/images/logo/fusion-360.png" alt="Logo de Fusion 360" 
class="logo--3rd-party">
    <i>Logo de Fusion 360</i>
</div>
mkdocs-only-end -->

[Fusion 360](https://www.autodesk.com/products/fusion-360/overview) es un programa de diseño 3D de Autodesk, con el cual pudimos diseñar las piezas en 3D y exportarlas al formato `.stl` para imprimir con mucha facilidad. Es muy versátil para dibujantes, ingenieros, fabricantes y para la creación de equipos, ya que tiene funciones de renderizado, diseño, pesaje de componentes, diseño de PCB, simulaciones, modelado de forma libre, etc.

Elegimos este programa porque es una solución "todo en uno" que combina el diseño, la fabricación, la ingeniería y el diseño de PCB, todo esto asistido por computadora, lo que hace todo mucho más cómodo.

## Planificación

### Jira

<!-- github-only-start -->
<p align="center">
	Logo de Jira
	<br>
	<i>Logo de Jira</i>
</p>
<!-- github-only-end -->

<!-- mkdocs-only-start
<div class="hcenter">
    <img src="/assets/images/logo/jira.png" alt="Logo de Jira" 
class="logo--3rd-party">
    <i>Logo de Jira</i>
</div>
mkdocs-only-end -->

[Jira](https://www.atlassian.com/software/jira) es una página web cuyo objetivo es la de organizar las tareas de un equipo de trabajo y asignarles una prioridad, básicamente es una página de organización de trabajo.

En nuestro caso, el uso de Jira nos permitió mantener el desarrollo de Klevor a un ritmo constante, ya que cada miembro del equipo tenía asignadas tareas específicas y un plazo para completarlas, lo que nos permitió avanzar de manera más eficiente y organizada.

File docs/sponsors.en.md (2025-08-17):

# Sponsors

Despite all the efforts from each of the team's members, we think that nothing that we achieved wouldn't be possible without the immense help from all of our sponsors:

## Viajes Giorgio

<!-- github-only-start -->
<p align="center">
	Viajes Giorgio's Logo
	<br>
	<i>Viajes Giorgio's Logo</i>
</p>
<!-- github-only-end -->

<!-- mkdocs-only-start
<div class="hcenter">
    <img src="/assets/images/sponsors/viajes-giorgio.png" alt="Viajes Giorgio's Logo" 
class="logo--sponsor">
    <i>Viajes Giorgio's Logo</i>
</div>
mkdocs-only-end -->

Viajes Giorgio is a travelling agency that specializes in domestic and international flights, and also offers general touristic advice, with accredited travel agent. Their commitment is to bring a quality service, adapting to each client's needs to guarantee a unique travelling experience.

- Instagram: [@viajesgiorgiooficial](https://www.instagram.com/viajesgiorgiooficial/)
- WhatsApp: [+593 99 429 2979](https://wa.me/593994292979)
- Location: [Centro Corporativo Zyra, Av. 6 de diciembre y Av. Portugal, Quito, Ecuador](https://maps.app.goo.gl/Vw3a9mdFkt4FSpa28)

## Nathaly's Star

<!-- github-only-start -->
<p align="center">
	Nathaly's Star's Logo
	<br>
	<i>Nathaly's Star's Logo</i>
</p>
<!-- github-only-end -->

<!-- mkdocs-only-start
<div class="hcenter">
    <img src="/assets/images/sponsors/nathalys-star.png" alt="Nathaly's Star's Logo" 
class="logo--sponsor">
    <i>Nathaly's Star's Logo</i>
</div>
mkdocs-only-end -->

Nathaly's Star is a fashion boutique specialized in high-quality clothes and accessories, focusing on latest trends and styles. Its commitment is to provide to their customers an unforgettable shopping experience, with products that stand out for their elegance and originality.

- Instagram: [@boutiquenathalysstar](https://www.instagram.com/boutiquenathalysstar/)
- Location (Maracaibo): [Local L-67, entre la entrada La Chinita y Sinamaica, Nivel Lago, Centro Sambil Maracaibo, Maracaibo, Venezuela](https://maps.app.goo.gl/rBUmZLRyckYVG9r38)
- Location (Ciudad Ojeda): [Centro Comercial Camino Real, Calle Vargas con Calle Bermúdez, Ciudad Ojeda, Venezuela](https://maps.app.goo.gl/X45idmxjfygE8ngX6)

## Steel C.A.

<!-- github-only-start -->
<p align="center">
	Steel C.A.'s Logo
	<br>
	<i>Steel C.A.'s Logo</i>
</p>
<!-- github-only-end -->

<!-- mkdocs-only-start
<div class="hcenter">
    <img src="/assets/images/sponsors/steel-ca.png" alt="Steel C.A.'s Logo" 
class="logo--sponsor">
    <i>Steel C.A.'s Logo</i>
</div>
mkdocs-only-end -->

Steel C.A. is a company dedicated to the manufacturing and marketing for steel products, offering innovative and high-quality solutions for a wide variety of industries. With a focus for the metalworking industry, Steel C.A. stands out for their commitment to the excellence and customer satisfaction, offering products that meet the highest standards of quality and durability.

- WhatsApp: [+58 412-6680683](https://wa.me/584126680683)

Thanks for every single of you to believe in us and helping in the making of Klevor!

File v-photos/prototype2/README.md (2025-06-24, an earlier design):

<h1 id="index">Índice</h1>

1. **[Introducción](#introduccion)**
2. **[Capas](#capas)**
    1. **[Primera Capa](#primera-capa)**
    2. **[Segunda Capa](#segunda-capa)**

<h1 id="introduccion">Introducción</h1> 

Este es un segundo prototipo de Klevor, donde se le hicieron correcciones
esenciales y se agregaron nuevos componentes que explicaremos detalladamente.

<h1 id="capas">Capas</h1>

<h2 id="primera-capa">Primera Capa</h2>

En esta primera capa, al igual que en nuestro primer prototipo, tenemos nuestro
sistema motriz, al cual no se le hicieron modificaciones. Este funciona como el
sistema mecánico de un automóvil, un mecanismo 4x4 de dos diferenciales (sistema
de engranajes cubiertos por una carcasa) conectados entre sí por un eje
transmisor. Nosotros conectamos nuestro
motor ([INJORA 48T](../../README.md/#componentes-injora-180-motor-48t)) a un
piñón que tiene el eje transmisor, esto hace que los diferenciales giren en un
mismo sentido y que por consecuencia, Klevor se mueva.

Una parte fundamental para nuestro robot es su sistema de cruce. Es basado en un
mecanismo Ackermann, que consiste en que las dos ruedas están conectadas por una
dirección o "sistema de trapecio", esto lo que hace es que, mediante una fuerza
que haga el cruce (en este caso nuestro
servomotor [INJORA 7 kg 2065](../../README.md/#componentes-injora-7kg-2065-micro-servo))
la dirección se mueva y eso hace girar ambas ruedas al mismo lado, debido a la
geometría y forma de trapecio que tiene la dirección, las ruedas no giran con el
mismo ángulo, sino que, la rueda interna respecto al cruce gira más que la rueda
externa.

Las ruedas para funcionar están conectadas a un muñón de dirección, luego a un "
palier" o "semieje" que pasa por dentro del muñón y se junta con la rueda para
que esta gire, el palier gira mientras está junto al diferencial.

<p align="center">
    Sistema Ackermann
</p>

En este diagrama se ve un ejemplo más claro de cómo funciona este sistema.
Describiremos a continuación el significado de cada término:

**ICR** (Centro Instantáneo de Rotación): Es el punto alrededor del cual el eje
delantero está girando.

**R**: Es el radio del giro del vehículo, medido desde el ICR hasta el centro
del eje trasero.

**L**: Es la distancia entre el eje delantero y el eje trasero de Klevor, o la
distancia de nuestro eje transmisor.

**B**: Es la distancia entre los muñones de dirección (La pieza en la que va la
rueda y se conecta a la dirección)

**a(i)**: Es el ángulo de giro de nuestra rueda interior respecto a la curva.

**a(o)**: Es el ángulo de nuestra rueda exterior respecto al giro.

Esto ilustra más la geometría de la dirección que permite que las ruedas
delanteras giren en ángulos diferentes y a su vez en la misma dirección,
consiguiendo así un giro eficiente.

Nuestro motor [INJORA 48T](../../README.md/#componentes-injora-180-motor-48t) es
el que se encarga de mover gran parte del sistema motriz, pero presentó una
falla al no tener el suficiente torque para mover el robot. Por esto tomamos la
decisión de hacer un sistema reductor de RPM, consta de un piñón que está en la
boquilla del motor y que se conecta a 2 piñones más junto al engranaje principal
del eje transmisor, reduciendo así la velocidad del motor, pero añadiendo más
fuerza al mismo.

Seguiremos explicando esta primera capa de nuestro robot. De componentes tiene
un [giroscopio](../../README.md/#gyroscope-gy-bno085) que ayuda al robot a
orientarse y así contar el número de vueltas que da, tiene una
batería [URGENEX 7.4](../../README.md/#componentes-urgenex-74v-battery) que
alimenta
al [INJORA MB100 20A mini ESC](../../README.md/#componentes-injora-mb100-20a-mini-esc)
que es un regulador de velocidad y a su vez también alimenta el motor INJORA 48T
y el servomotor INJORA 7 kg 2065.

<h3 id="por-que">¿Por qué diseñamos así nuestro chasis?</h3>

Este chasis es una modificación de la primera capa del primer prototipo de
Klevor. Decidimos modificarla por el peso, reduciendo el espacio por componentes
que ya no están, esta primera capa también está diseñada con esa forma debido a
las piezas de kits que no son modificables, como lo son los diferenciales, los
muñones de dirección y el eje transmisor. Así hicimos un espacio a medida para
cada componente. Esta también es la razón por la que diseñamos toda la parte de
conexión de las ruedas (Ruedas, Semiejes y cajas de diferenciales).

<h2 id="segunda-capa">Segunda Capa</h2>

Esta es la capa donde más cambios se hicieron, anteriormente aquí teníamos los
sensores ToF (Time of Flight), pero fueron reemplazados por
el [RPLidar C1](../../README.md/#componentes-rplidar-c1) un sensor que mediante
un láser infrarrojo nos permite detectar distancias de hasta 12 metros en los
360 grados, cosa que corrige el mal funcionamiento de los anteriores sensores,
que daban lecturas erróneas y tenían un rango de detección muchísimo más corto.
Decidimos colocarlo al revés para que evitar que tenga lecturas erróneas debido
a que su láser pasaría por encima de la pared de la pista.

En esta parte superior también está el
microcontrolador ([Raspberry Pi Pico 2](../../README.md/#componentes-raspberry-pi-pico-2-wh))
y el
microprocesador ([Raspberry Pi 5](../../README.md/#componentes-raspberry-pi-5)),
además de la alimentación de los mismos, que es un power bank marca Harvic® de
10000 mAh y 22.5 W, este se conecta a la Raspberry Pi 5 y a su vez, envía parte
del voltaje al RPLIDAR; la Raspberry Pi Pico 2 y
la [Raspberry Cam Module 3 Wide](../../README.md/#componentes-raspberry-pi-camera-module-3-wide),
que es la cámara que nos ayudará a detectar los colores de los bloques en el
desafío cerrado.

<h3 id="por-que">¿Por qué diseñamos así la parte superior?</h3>

La parte superior cambió drásticamente en cuanto a diseño, los cambios que
hicimos fueron:

**Crear un espacio en la parte frontal**: Esto lo hicimos para colocar el
RPLIDAR con el mayor ángulo de visión posible

**Recortar bordes**: Para reducir peso y espacio innecesario

**Orificios**: Con el fin de poder conectar cables con la parte de abajo, esto
nos da más facilidad a la hora de ensamblar a Klevor

**Soporte Raspberry Pi Cam 3**: Luego de probar qué ángulo de colocación era el
mejor para la cámara decidimos hacer un soporte completamente fijo. Aunque
pensamos cambiarlo más adelante.

Decidimos eliminar también la tercera capa que tenía el primer prototipo, ya que
pudimos resumir todos los componentes en una única superficie.

 <table>
     <tr>
         <td>
             <p align="center">
                 Vista delantera
             </p>
             <p align="center">
                 <i>Vista delantera</i>
             </p>
         </td>
         <td>
             <p align="center">
                 Vista Trasera
             </p>
             <p align="center">
                 <i>Vista trasera</i>
             </p>
         </td>
     </tr>
     <tr>
         <td>
             <p align="center">
                 Vista derecha
             </p>
             <p align="center">
                 <i>Vista derecha</i>
             </p>
         </td>
         <td>
             <p align="center">
                 Vista izquierda
             </p>
             <p align="center">
                 <i>Vista izquierda</i>
             </p>
         </td>
     </tr>
     <tr>
       <td>
             <p align="center">
                 Vista superior
             </p>
             <p align="center">
                 <i>Vista superior</i>
             </p>
         </td>
         <td>
             <p align="center">
                 Vista inferior
             </p>
             <p align="center">
                 <i>Vista inferior</i>
             </p>
         </td>
     </tr>
 </table>

Cabe destacar que todos nuestros diseños 3D fueron hechos en el programa "
Fusion360". Fusion360 es una programa de Autodesk, que se utiliza para el diseño
y la fabricación de productos. Es muy versátil para dibujantes, ingenieros,
fabricantes y para la creación de equipos, ya que tiene funciones de
renderizado, diseño, pesaje de componentes, diseño de PCB, Simulaciones,
modelado de forma libre, etc.

Elegimos este programa porque es una solución "todo en uno" que combina el
diseño, la fabricación, la ingeniería y el diseño de PCB, todo esto asistido por
computadora, lo que hace todo mucho más cómodo.

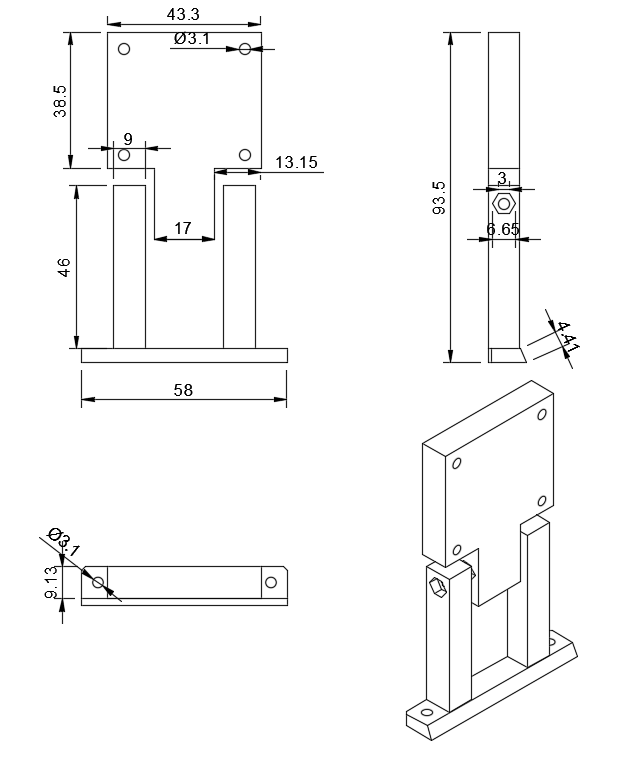
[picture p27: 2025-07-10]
docs/assets/images/github/models/2d-designs/prototype1/camera-mounting-prototype1.png

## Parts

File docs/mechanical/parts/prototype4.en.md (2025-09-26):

# Prototype 4 {:#prototype4}

## Chassis {:#Chassis}

<!-- github-only-start -->
<p align="center">
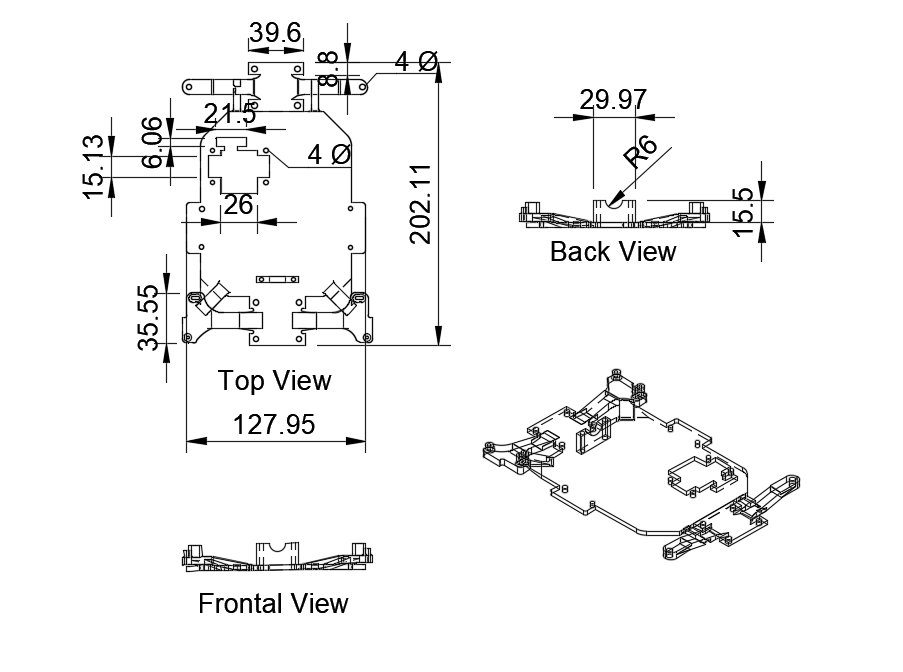
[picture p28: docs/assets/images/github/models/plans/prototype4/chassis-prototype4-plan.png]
Chassis
	
	<br>
	<i>Chassis</i>
</p>
<!-- github-only-end -->

<!-- mkdocs-only-start
<div class="hcenter">
	<img src="../../assets/images/github/models/plans/prototype4/chassis-prototype4-plan.png" alt="Chassis" 
class="mechanical-image">
	<i>Chassis</i>
</div>
mkdocs-only-end -->

In this prototype, we decided to make just one layer that serves as a base for all the components. This change was possible because, unlike the previous prototypes, we didn't need the RPM Reduction System, which was a pretty big component.

The main objective for this chassis was to improve the functioning of the motor system. The new wheels are 30mm larger in diameter, which was a problem, if we just implemented them like that, the entire robot would rise. This was a big inconvenience for the RPLiDAR, because, if it was high enough, it couldn't detect the obstacles nor the walls, to avoid this problem, we designed the chassis so that it was a lowered base with 4 raised points in the corners. Thanks to these high points, we can connect the wheels in the higher corners, while the rest of the components, including the RPLiDAR are placed at a lower height.

Aside from solving the height problem, this chassis' special design has another key benefit, it allows that the wheels had a bigger turning angle. With this upgrade, the robot has an advantage against the other prototypes, which offers a great advantage in the game field.

## Servo base

<!-- github-only-start -->
<p align="center">
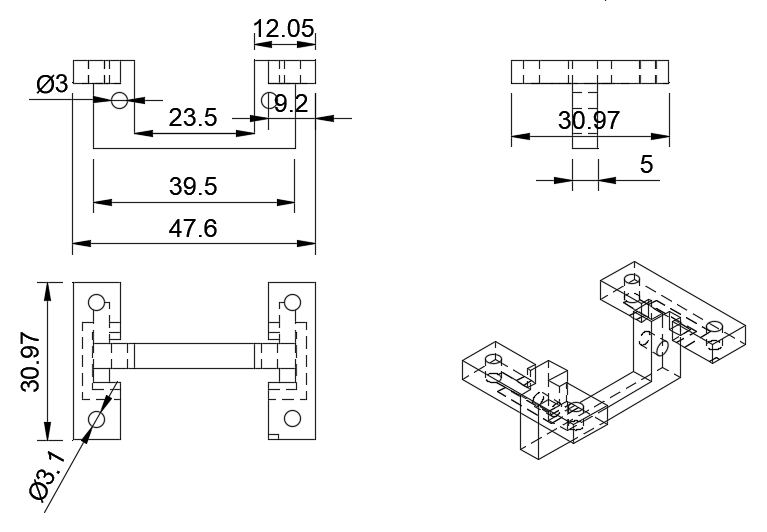
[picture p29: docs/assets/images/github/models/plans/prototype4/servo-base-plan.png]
Servo base
	
	<br>
	<i>Servo base</i>
</p>
<!-- github-only-end -->

<!-- mkdocs-only-start
<div class="hcenter">
	<img src="../../assets/images/github/models/plans/prototype4/servo-base-plan.png" alt="Servo base" 
class="mechanical-image">
	<i>Servo base</i>
</div>
mkdocs-only-end -->

This part was designed to be mounted directly on the servomotor, and afterwards, be mounted onto the chassis, we built it like this because we needed the servomotor to be low, so that when turning the servo, it wouldn't crash with the transmission shaft, and it had enough space to use all of the turning angle that Klevor has.

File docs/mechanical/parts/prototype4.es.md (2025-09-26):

# Prototipo 4 {:#prototype4}

## Chasis {:#Chassis}

<!-- github-only-start -->
<p align="center">
	Chasis
	<br>
	<i>Chasis</i>
</p>
<!-- github-only-end -->

<!-- mkdocs-only-start
<div class="hcenter">
	<img src="../../assets/images/github/models/plans/prototype4/chassis-prototype4-plan.png" alt="Chasis" 
class="mechanical-image">
	<i>Chasis</i>
</div>
mkdocs-only-end -->

En este prototipo, decidimos hacer un solo chasis que sirva como base para todos los componentes. Este cambio fue posible porque a diferencia de los modelos anteriores, ya no necesitamos el sistema de reducción de RPM, un sistema que antes ocupaba bastante espacio.

El objetivo principal de este nuevo chasis era mejorar el funcionamiento del sistema motriz. Las nuevas ruedas que usamos son 30mm más grandes en diámetro, lo que representaba un problema, si solamente las colocábamos, el robot completo se elevaría. Esto sería un gran inconveniente para el RPLiDAR, ya que si su altura aumenta demasiado, podría no detectar los obstáculos que están en la pista, para evitar este problema, diseñamos el chasis con una base que tiene cuatro puntos elevados específicamente en las esquinas. De esta manera, las ruedas se colocan en estos puntos más altos, mientras que el resto de los componentes, incluido el RPLidar, se mantienen a una altura baja.

Además de resolver el problema de la altura, este diseño especial de la base tiene otro beneficio clave, permite que las ruedas tengan un mayor ángulo de giro. Con esta mejora, el robot tiene una ventaja con respecto a los prototipos anteriores, lo que le da una gran ventaja en la pista.

## Base del Servomotor

<!-- github-only-start -->
<p align="center">
	Servo base
	<br>
	<i>Base del servomotor</i>
</p>
<!-- github-only-end -->

<!-- mkdocs-only-start
<div class="hcenter">
	<img src="../../assets/images/github/models/plans/prototype4/servo-base-plan.png" alt="Servo base" 
class="mechanical-image">
	<i>Base del servomotor</i>
</div>
mkdocs-only-end -->

Esta pieza fue diseñada para colocarse directamente en el servomotor, y posteriormente ser fijado en el chasis, lo hicimos así porque necesitabamos que el servomotor estuviera en un nivel bajo, para que al hacer los cruces no chocara con el eje de transmisión, y tuviera el espacio suficiente como para poder aprovechar al máximo el nuevo ángulo de giro que tiene Klevor.

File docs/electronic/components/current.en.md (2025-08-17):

# Current Components

Here is all of Klevor's components and their respective description.

## Raspberry Pi 5 (16GB RAM)

<!-- github-only-start -->
<p align="center">
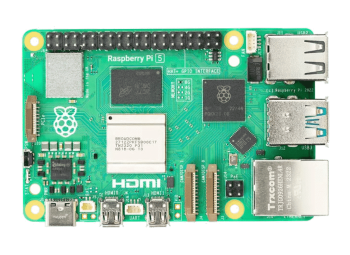
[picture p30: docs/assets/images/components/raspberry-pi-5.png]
Raspberry Pi 5
	
	<br>
	<i>Raspberry Pi 5</i>
</p>
<!-- github-only-end -->

<!-- mkdocs-only-start
<div class="hcenter">
    <img src="/assets/images/components/raspberry-pi-5.png" alt="Raspberry Pi 5" 
class="component-image">
    <i>Raspberry Pi 5</i>
</div>
mkdocs-only-end -->

Built with an 64-bit ARM Cortex-A76 processor, clocked at 2.4Ghz [[1](#raspberry-pi-5-datasheet)]. The Raspberry Pi 5 functions as our main computer, there are multiple reasons as to why we decided to use the Raspberry Pi 5, for example:

-**Compatibility**: Alongside choosing the Raspberry Pi 5 as our main computer, there are several other Raspberry components that also were selected for Klevor, which makes the implementation easier since those components are part of the same ecosystem.

-**Power**: The Raspberry Pi 5 is one of the fastest and most powerful single-board computers (SBC) available to the market, this helps us a lot to properly execute the more-demanding tasks, like the real-time image processing, used for the Closed Challenge.

-**Portability**:  The Raspberry Pi 5 is also a very light-weight option for Klevor, weighing around 60g, being one of the lightest components on this prototype [[1](#raspberry-pi-5-datasheet)].

| **Measurement** | **Value** |
|---|---|
| Length | 85 mm |
| Height | 58.9 mm |
| Width | 56 mm |
| Weight | 46 g |

## Raspberry Pi Camera Module 3 Wide

<!-- github-only-start -->
<p align="center">
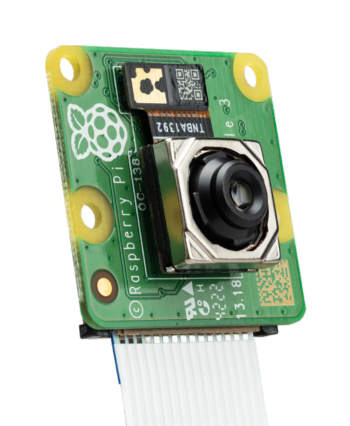
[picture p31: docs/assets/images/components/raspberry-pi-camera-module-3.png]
Raspberry Pi Camera Module 3
	
	<br>
	<i>Raspberry Pi Camera Module 3</i>
</p>
<!-- github-only-end -->

<!-- mkdocs-only-start
<div class="hcenter">
    <img src="/assets/images/components/raspberry-pi-camera-module-3.png" alt="Raspberry Pi Camera Module 3" 
class="component-image">
    <i>Raspberry Pi Camera Module 3</i>
</div>
mkdocs-only-end -->

The Raspberry Pi Camera Module 3 Wide is our preferred camera, as the rest of the Raspberry components, this camera is also small and pretty lightweight, however, just because it is small, it doesn't mean it can't perform, this camera is capable to record at 1536 x 864p120 [[2](#raspberry-pi-camera-module-3-geek-factory)] | [[3](#raspberry-pi-camera-documentation)], we decided to use this specific model, due to its Horizontal FoV which is 102 degrees, allowing Klevor to see all the field, which is a huge advantage for the Closed Challenge. 

| **Measurement** | **Value** |
|---|---|
| Length | 24 mm |
| Height | 25 mm |
| Width | 12.4 mm |
| Weight | 4 g |

## Raspberry Pi AI HAT+ (26 TOPS)

<!-- github-only-start -->
<p align="center">
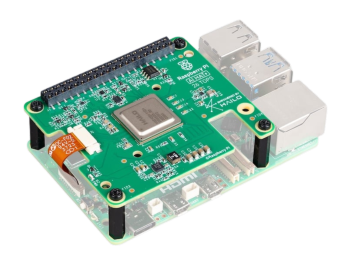
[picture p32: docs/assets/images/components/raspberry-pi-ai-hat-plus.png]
Raspberry Pi AI HAT+ 26 TOPS
	
	<br>
	<i>Raspberry Pi AI HAT+ 26 TOPS</i>
</p>
<!-- github-only-end -->

<!-- mkdocs-only-start
<div class="hcenter">
    <img src="/assets/images/components/raspberry-pi-ai-hat-plus.png" alt="Raspberry Pi AI HAT+ 26 TOPS" 
class="component-image">
    <i>Raspberry Pi AI HAT+ 26 TOPS</i>
</div>
mkdocs-only-end -->

The Raspberry Pi 5 is capable to perform real-time image processing, however, the speed at which it performs the task wasn't enough, because of this, we decided to implement the AI HAT+ to the Raspberry Pi 5 to reach our desired speed.

The Raspberry Pi AI HAT+ has two versiones, a 13 Trillion Operations per Seconds (TOPS) and a 26 TOPS version [[4](#raspberry-pi-ai-hat-documentation)]. As we previously mentioned, Klevor has a 26 TOPS Raspberry Pi AI HAT+, thanks to this specific component, Klevor is can analyze 30 images per second with a 640 pixels by 640 pixels resolution.

| **Measurement** | **Value** |
|---|---|
| Length | 65 mm |
| Height | 5.5 mm |
| Width | 56 mm |
| Weight | 9.07 g |

## Raspberry Pi Pico 2 WH

<!-- github-only-start -->
<p align="center">
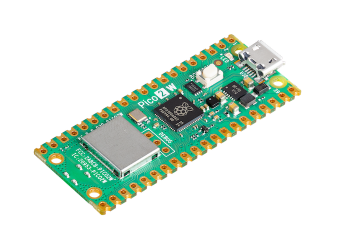
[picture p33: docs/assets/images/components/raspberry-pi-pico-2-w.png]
Raspberry Pi Pico 2 W
	
	<br>
	<i>Raspberry Pi Pico 2 W</i>
</p>
<!-- github-only-end -->

<!-- mkdocs-only-start
<div class="hcenter">
    <img src="/assets/images/components/raspberry-pi-pico-2-w.png" alt="Raspberry Pi Pico 2 W" 
class="component-image">
    <i>Raspberry Pi Pico 2 W</i>
</div>
mkdocs-only-end -->

Built over the RP2350 chip [[5](#raspberry-pi-pico-2-wh-datasheet)], the Raspberry Pi Pico 2 W is our single-board microcontroller, while being a light-weight and relatively small component, it also allows for a quick integration with the other Raspberry components, the main reason behind this quick integration is due to the serial communication required to properly manage all of Klevor's resources. Establishing a serial communication between a Raspberry Pi 5 and a Raspberry Pi Pico 2 W is much quicker than a Raspberry Pi 5 and a single-board microcontroller made by a different manufacturer.

Alongside this, the Raspberry Pi 5, offers a 150 Mega-hertz (Mhz) clock rate, which is vastly similar when compared to other single-board microcontroller with the similar physical dimensions as the Raspberry Pi Pico 2 W.

We also decided to settle on the model with an integrated WiFi module, because, with this, we are able to debug any issues much quicker, or just knowing what is exactly Klevor thinking during practice rounds, without having the need to implement multiple LEDs to debug, resulting in a much more clean final product.

| **Measurement** | **Value** |
|---|---|
| Length | 51 mm |
| Height | 12 mm |
| Width | 21 mm |
| Weight | 6 g |

## RPLiDAR C1

<!-- github-only-start -->
<p align="center">
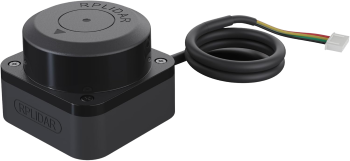
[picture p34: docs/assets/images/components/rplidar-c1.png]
RPLiDAR C1
	
	<br>
	<i>RPLiDAR C1</i>
</p>
<!-- github-only-end -->

<!-- mkdocs-only-start
<div class="hcenter">
    <img src="/assets/images/components/rplidar-c1.png" alt="RPLiDAR C1" 
class="component-image">
    <i>RPLiDAR C1</i>
</div>
mkdocs-only-end -->

The RPLidar C1 is a 360 degree laser scanner, this scanner is capable of detecting objects within a 12-meter range, whilst having a blind range that is about 5cm [[6](#rplidar-c1-robot-shop)] | [[7](#rplidar-c1-datasheet)], all of these factors make the RPLiDAR C1 a pretty good option to guide Klevor around the game field.

This RPLiDAR C1 allows Klevor to pinpoint his exact location in the game field, thanks to the immense amount of data that the RPLiDAR C1 offers.

| **Measurement** | **Value** |
|---|---|
| Length | 55.6 mm |
| Height | 41.3 mm |
| Width | 55.6 mm |
| Weight | 110 g |

Technical specifications:

| **Specifications** | **Value** |
|---|---|
| Distance Range | White：0.05~12m (70% Reflectivity); Black：0.05~6m (10% Reflectivity) |
| Sample Rate | 5 kHz |
| Angle Resolution | 0,72° |
| Pitch Angle | 0°-1,5° |

## Shargeek Storm 2

<!-- github-only-start -->
<p align="center">
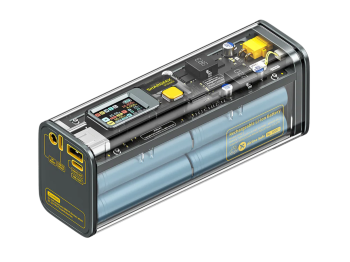
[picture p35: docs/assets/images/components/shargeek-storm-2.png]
Shargeek Storm 2
	
	<br>
	<i>Shargeek Storm 2</i>
</p>
<!-- github-only-end -->

<!-- mkdocs-only-start
<div class="hcenter">
    <img src="/assets/images/components/shargeek-storm-2.png" alt="Shargeek Storm 2" 
class="component-image">
    <i>Shargeek Storm 2</i>
</div>
mkdocs-only-end -->

The Shargeek Storm is a Power Bank with pretty interesting characteristics [[8](#shargeek-storm-2-amazon)] | [[9](#shargeek-storm-2-100w-power-bank)] such as:

- 25600 mAh capacity.
- 100 W Power Delivery (PD) Input and Output.
- Integrated IPS screen
- Fully recharged in just 90 minutes.

All of these factors make the Shargeek Storm 2 to be a perfect portable power supply for the Raspberry Pi 5.

However, the Shargeek Storm 2's weight is considerable enough to the point where other smaller and lighter Power Banks might be a better option for the overall product.

| **Measurement** | **Value** |
|---|---|
| Length | 150.8 mm  |
| Height | 58.9 mm |
| Width | 45.9 mm |
| Weight | 579 g |

## INJORA 180 Motor 48T

<!-- github-only-start -->
<p align="center">
	INJORA 180 Motor 48T
	<br>
	<i>INJORA 180 Motor 48T</i>
</p>
<!-- github-only-end -->

<!-- mkdocs-only-start
<div class="hcenter">
    <img src="/assets/images/components/injora-180-motor-48t.png" alt="INJORA 180 Motor 48T" 
class="component-image">
    <i>INJORA 180 Motor 48T</i>
</div>
mkdocs-only-end -->

The INJORA 180 Motor 48T is a motor designed for the quick radio-controller cars, these cars usually have similar physical specifications as Klevor's which is why we thought that this motor would be a great incorporation. Due to its relatively small size and relatively low operative voltage (7.4 Volts, we considered to use 12V, even some 24V options for Klevor) and also a pretty  [[10](#injora-180-48t-amazon)].

With all of these advantages, we consider than a DC motor with an integrated Encoder (which means, that it is capable to count all the rotations) would be far better, mostly because it allows to perfectly regulate all of Klevor's movements, instead of assigning the motor to move for a certain time which allows for any error to happen (mostly because of a "lag spike"), instead, with an Encoder, is easier, instead of assigning the motor to move for a certain time, you can assign it to move a certain distance or rotations, even if a "lag spike" occurs, the motor can acknowledge how much distance is left, or if it overshoots the distance, allowing for a more controlled route.

| **Measurement** | **Value** |
|---|---|
| Length | 42.7 mm |
| Height | 10 mm |
| Widht | 15 mm |
| Weight | 38 g |

Mechanical specifications:

| **Specification**  | **Value** |
|---|---|
| No-load speed | 20500rpm  |
| No-load current | 0.48A |

## INJORA MB100 20A mini ESC

<!-- github-only-start -->
<p align="center">
	INJORA MB100 20A Mini ESC
	<br>
	<i>INJORA MB100 20A Mini ESC</i>
</p>
<!-- github-only-end -->

<!-- mkdocs-only-start
<div class="hcenter">
    <img src="/assets/images/components/injora-mb100-mini-esc-20a.png" alt="INJORA MB100 20A Mini ESC" 
class="component-image">
    <i>INJORA MB100 20A Mini ESC</i>
</div>
mkdocs-only-end -->

The INJORA MB100 20A mini ESC is an Electronic Speed Control [[11](#injora-mb100-r80-amazon)], normally this ESC is paired with any INJORA motor, this ESC specifically allows for the connection between the INJORA 180 Motor 48T and the Raspberry Pi Pico 2.

Thanks to this little device, we can assure a safe and effective connection between the motor and the Pico 2, without the need of a bigger device (for example an H-bridge L298N) to serve the exact same purpose. Also, this mini ESC is capable of resisting the peak currents (which can be as high as 100A) that the INJORA 180 Motor 48T can consume.

On top of all, it is a pretty easy component to configure thanks to libraries like `adafruit_motor` which allows to configure the motor as if it is a Continuous Rotation Servo thanks to the `servo` module.

Also, this ESC has a BEC (Battery Eliminator Circuit) normally, this is intended to be used to power the receiver for a radio-controlled car, in Klevor's case we use it to power the [INJORA 7Kg 2065 Micro Servo](#injora-7-kg-2065-micro-servo), without the need to implement a third battery or a second alimentation from the same battery.

| **Measurement** | **Value** |
|---|---|
| Length | 37 mm |
| Height | 22 mm |
| Width | 10 mm |
| Weight | 15 g |

Mechanical specifications:

| **Specifications**  | **Value** |
|---|---|
| Motor Type Support: | Brushed Motor ( 030 / 050 / 130 / 180 / 370 ) |
| BEC Output: | 6V/3A (linear Mode) |

## URGENEX 7.4 V Battery

<!-- github-only-start -->
<p align="center">
	URGENEX 7.4 V Battery
	<br>
	<i>URGENEX 7.4 V Battery</i>
</p>
<!-- github-only-end -->

<!-- mkdocs-only-start
<div class="hcenter">
    <img src="/assets/images/components/urgenex-7-4v-3000mah.png" alt="URGENEX 7.4 V Battery" 
class="component-image">
    <i>URGENEX 7.4 V Battery</i>
</div>
mkdocs-only-end -->

The URGENEX 7.4V Battery is our second battery, which is used to power the INJORA MB100 mini ESC, which also powers the INJORA 180 Motor 48T and the INJORA 7kg 2065 Micro Servo, on top of this, it is a rechargeable battery, which turns it into a pretty solid option to power the principal motor.

Honestly, any 7.4V would perfectly work with the INJORA MB100 mini ESC, we just decided to use the URGENEX 7.4V Battery because it is a high quality battery, and it works pretty well with the INJORA 180 Motor, specially with the peak current usage that it can reach, however these peaks in usage might me too much for the Shargeek Storm 2, so we decided that it was not worth the risk and just powered the motor separately.

Another factor to take into consideration is the high capacity this battery offers when compared to the rest of the market, which is 3000mAh [[12](#urgenex-3000-mah-amazon)].

| **Measurement** | **Value** |
|---|---|
| Length | 37 mm |
| Height | 70 mm |
| Width | 19 mm |
| Weight | 103 g |

## INJORA 7 kg 2065 Micro Servo

<!-- github-only-start -->
<p align="center">
	INJORA 7 kg 2065 Micro Servo
	<br>
	<i>INJORA 7 kg 2065 Micro Servo</i>
</p>
<!-- github-only-end -->

<!-- mkdocs-only-start
<div class="hcenter">
    <img src="/assets/images/components/injora-7kg-2065-micro-servo.png" alt="INJORA 7 kg 2065 Micro Servo" 
class="component-image">
    <i>INJORA 7 kg 2065 Micro Servo</i>
</div>
mkdocs-only-end -->

The INJORA 7kg 2065 Micro Servo is the servomotor assigned to control Klevor's direction system, we decided to use this model, due to its small size and low weight, also offering an accuracy more than enough to control Klevor [[13](#injora-7kg-2065-amazon)].

However, the main aspect that made us choose the INJORA 7kg 2065 was the insane accuracy with such a reduced size, which is crucial for a competition like this.

Thanks to the aforementioned library,  the `adafruit_motor` with its `servo` modulo, allows us to configure the servo to our choice, which simplifies the usage of functions to control the servo to be much easier to read without risking the program's performance.

| **Measurement** | **Value** |
|---|---|
| Length | 23 mm |
| Height | 25.8 mm |
| Width | 13 mm |
| Weight | 20 g |

## 9-Axis IMU Gyroscope GY-BNO085

<!-- github-only-start -->
<p align="center">
	BNO085
	<br>
	<i>BNO085</i>
</p>
<!-- github-only-end -->

<!-- mkdocs-only-start
<div class="hcenter">
    <img src="/assets/images/components/bno08x.png" alt="BNO085" 
class="component-image">
    <i>BNO085</i>
</div>
mkdocs-only-end -->

The GY-BNO085 is an inertial measurement unit (IMU) with 9 Degrees of Freedom, gyroscopes in general are often used for tasks that require a precise tracking for a certain movement. We decided to use this gyroscope for Klevor to gain more autonomy on the field, specially when turning, since this sensor can help Klevor align perfectly and adjust,

Aside from this, we can also use the gyroscope and a way to count the turns Klevor has done across the round, on both the Open Challenge and the Closed Challenge this is crucial, since Klevor can know if its aligned, or it is deviating from it due to any mechanical issue, in which case, the gyroscope can detect exactly how much Klevor needs to turn, which is crucial to avoid hitting the wall and potentially getting the round disqualified.

Now the way that we implemented the gyroscope is also relatively simple, the gyroscope is always updating data asynchronously every 50 milliseconds, and Klevor keeps track with two variables, `yaw_deg` (which represents the difference in degrees on its yaw orientation respective to when it started, which is basically just the gyroscope data but forced to start at 0 degrees to make it easier to code) and `relative_yaw` which uses `yaw_deg` to assign itself a value, this variable works differently since `yaw_deg` normally resets from -180 straight to 180 degrees, what `relative_yaw` does instead is just add or subtract 360 degrees to itself whenever `yaw_deg` resets.

We implement `relative_yaw` to keep track of the turns made on the track, we can simply divide it by 90 and round down (for example, if the division is equal to 10.57, it will be perceived as if Klevor has made 10 turns as is in the middle of a turn, or it is deviating from the middle), whenever this division is equal to either -12 or 12, we know that Klevor must park soon, in the Open Challenge it just moves forward until it detects a distance that is about 1.5m on front, and in the Closed Challenge it starts to activate the parking detection.

| **Measurement** | **Value** |
|---|---|
| Length | 25.75 mm  |
| Height | 15.5 mm |
| Width | 1.8 mm |
| Weight | 3 g |

# References

1. *Raspberry Pi 5
   Datasheet*. (2025). Raspberry Pi Ltd. <a id="raspberry-pi-5-datasheet" href="https://datasheets.raspberrypi.com/rpi5/raspberry-pi-5-product-brief.pdf">https://datasheets.raspberrypi.com/rpi5/raspberry-pi-5-product-brief.pdf</a>

2. *Raspberry Pi camera module 3 (standard | wide |
   NOIR)*. (2025). GeekFactory. <a id="raspberry-pi-camera-module-3-geek-factory" href="https://www.geekfactory.mx/producto/raspberry-pi-camera-module-3/">https://www.geekfactory.mx/producto/raspberry-pi-camera-module-3/</a>

3. *Raspberry Pi Camera
   Documentation*. (2025). Raspberry Pi Ltd. <a id="raspberry-pi-camera-documentation" href="https://www.raspberrypi.com/documentation/accessories/camera.html">https://www.raspberrypi.com/documentation/accessories/camera.html</a>

4. *Raspberry Pi AI HAT+
   Documentation*. (2025). Raspberry Pi Ltd. <a id="raspberry-pi-ai-hat-documentation" href="https://www.raspberrypi.com/documentation/accessories/ai-hat-plus.html">https://www.raspberrypi.com/documentation/accessories/ai-hat-plus.html</a>

5. *Raspberry Pi Pico 2 WH
   Datasheet*. (2025). Raspberry Pi Ltd. <a id="raspberry-pi-pico-2-wh-datasheet" href="https://datasheets.raspberrypi.com/pico/pico-2-product-brief.pdf">https://datasheets.raspberrypi.com/pico/pico-2-product-brief.pdf</a>

6. *Escáner Láser DTOF 360° SLAMTEC RPLIDAR
   C1*. (2025). RobotShop. <a id="rplidar-c1-robot-shop" href="https://www.robotshop.com/es/products/escaner-laser-dtof-360-slamtec-rplidar-c1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">https://www.robotshop.com/es/products/escaner-laser-dtof-360-slamtec-rplidar-c1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</a>

7. *RPLidar C1 360 ToF LiDAR
   Datasheet*. (2025). RobotShop. <a id="rplidar-c1-datasheet" href="https://cdn.robotshop.com/media/R/Rpk/RB-Rpk-35/pdf/rp-lidar-360-tof-lidar-datasheet.pdf">https://cdn.robotshop.com/media/R/Rpk/RB-Rpk-35/pdf/rp-lidar-360-tof-lidar-datasheet.pdf</a>

8. *Shargeek Storm 2, banco de energía para portátil de 100 W, cargador portátil
   de 25600 mAh, primer banco de energía transparente del mundo con pantalla
   IPS, Samsung Galaxy, MacBook y
   más*. (2025). Amazon. <a id="shargeek-storm-2-amazon" href="https://www.amazon.es/Shargeek-port%C3%A1til-cargador-transparente-pantalla/dp/B09NY8GN76">https://www.amazon.es/Shargeek-port%C3%A1til-cargador-transparente-pantalla/dp/B09NY8GN76</a>

9. *Shargeek Storm 2, 100W Portable Power
   Bank*. (2025). Sharge Technology (Shenzhen) Co., Ltd. <a id="shargeek-storm-2-100w-power-bank" href="https://docs.google.com/gview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">https://docs.google.com/gview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</a>

10. *INJORA Motor Cepillado 180 48T con Piñón de Acero Inoxidable, Conector
    JST-PH2.0 para Upgrade 1/18 RC Crawler Redcat
    Ascent-18*. (2025). Amazon. <a id="injora-180-48t-amazon" href="https://www.amazon.es/INJORA-Cepillado-Inoxidable-JST-PH2-0-Ascent-18/dp/B0D97YNMLG?ref_=ast_sto_dp">https://www.amazon.es/INJORA-Cepillado-Inoxidable-JST-PH2-0-Ascent-18/dp/B0D97YNMLG?ref_=ast_sto_dp</a>

11. *INJORA MB100-R80 20A Brushed Mini ESC con Motor 180 de 48T para
    Actualización TRX4M 1/18 RC
    Crawler*. (2025). Amazon. <a id="injora-mb100-r80-amazon" href="https://www.amazon.es/INJORA-MB100-Brushed-Actualizaci%C3%B3n-Crawler/dp/B0CXT74XV6?ref_=ast_sto_dp">https://www.amazon.es/INJORA-MB100-Brushed-Actualizaci%C3%B3n-Crawler/dp/B0CXT74XV6?ref_=ast_sto_dp</a>

12. *URGENEX 3000mAh 7.4 V Li-ion Battery with Dean-Style T Plug 2S Rechargeable
    RC Battery Fit for WLtoys 4WD High Speed RC Cars and Most 1/10, 1/12, 1/16
    Scale RC Cars Trucks with 7.4V Battery
    Charger*. (2025). Amazon. <a id="urgenex-3000-mah-amazon" href="https://www.amazon.com/URGENEX-Bater%C3%ADa-enchufe-recargable-velocidad/dp/B0CYNVSN7W?ref_=ast_sto_dp">https://www.amazon.com/URGENEX-Bater%C3%ADa-enchufe-recargable-velocidad/dp/B0CYNVSN7W?ref_=ast_sto_dp</a>

13. *INJORA 7 kg 2065 Digital Servo Waterproof High Voltage Sub-Micro Shift
    Servo for TRX4 TRX6 SCX10 III 1/10 RC Crawler
    Car,1PCS*. (2025). Amazon. <a id="injora-7kg-2065-amazon" href="https://www.amazon.com/digital-impermeable-voltaje-Sub-Micro-Crawler/dp/B0BLBMVYCW?ref_=ast_sto_dp">https://www.amazon.com/digital-impermeable-voltaje-Sub-Micro-Crawler/dp/B0BLBMVYCW?ref_=ast_sto_dp</a>

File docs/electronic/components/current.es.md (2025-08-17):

# Componentes Actuales

A continuación, está la descripción de todos los componentes principales de Klevor.

## Raspberry Pi 5 (16GB RAM)

<!-- github-only-start -->
<p align="center">
	Raspberry Pi 5
	<br>
	<i>Raspberry Pi 5</i>
</p>
<!-- github-only-end -->

<!-- mkdocs-only-start
<div class="hcenter">
    <img src="/assets/images/components/raspberry-pi-5.png" alt="Raspberry Pi 5" 
class="component-image">
    <i>Raspberry Pi 5</i>
</div>
mkdocs-only-end -->

Equipada con un procesador ARM Cortex-A76 de 64 bits a 2.4 GHz [[1](#raspberry-pi-5-datasheet)]. La Raspberry Pi 5 es nuestro controlador principal de elección, decidimos usar a la Raspberry Pi 5 debido a múltiples factores, entre ellos:

- **Compatibilidad**: Existen muchos componentes de Klevor (como la Camera Module 3 Wide) que a su vez pertenecen al ecosistema Raspberry, lo que hace que implementarlos a la Raspberry Pi 5 no requiera tanto esfuerzo.

- **Potencia**: La Raspberry Pi 5 es uno de los computadores portátiles más potentes actualmente, gracias a esto, funciones demandantes como lo es el procesamiento de imágenes en tiempo real, son fácilmente realizables por una Raspberry Pi 5.

- **Portabilidad**: La Raspberry Pi 5 destaca entre los controladores, ya que no es una computadora bastante pesada, apenas llegando a los 60 g, hace que incorporarlo a Klevor sea una opción prácticamente segura [[1](#raspberry-pi-5-datasheet)].

| **Medida** | **Valor** |
|---|---|
| Largo | 85 mm |
| Alto | 58.9 mm |
| Ancho | 56 mm |
| Peso | 46 g |

## Raspberry Pi Camera Module 3 Wide

<!-- github-only-start -->
<p align="center">
	Raspberry Pi Camera Module 3
	<br>
	<i>Raspberry Pi Camera Module 3</i>
</p>
<!-- github-only-end -->

<!-- mkdocs-only-start
<div class="hcenter">
    <img src="/assets/images/components/raspberry-pi-camera-module-3.png" alt="Raspberry Pi Camera Module 3" 
class="component-image">
    <i>Raspberry Pi Camera Module 3</i>
</div>
mkdocs-only-end -->

La Raspberry Pi Camera Module 3 Wide es nuestra elección de preferencia, como los demás componentes Raspberry, esta se destaca por ser bastante ligera y portátil, ya que, pues es una cámara bastante pequeña, midiendo apenas 25 mm × 24 mm × 12.4 mm y pesando 4 gramos, sin perder absolutamente ni una pizca de eficiencia, porque puede grabar a 1536 x 864p120, ahora bien, decidimos utilizar la versión Wide por su campo de visión horizontal de 102 grados [[2](#raspberry-pi-camera-module-3-geek-factory)] | [[3](#raspberry-pi-camera-documentation)], porque nos permite tener un rango de visión óptimo para poder detectar todos los obstáculos de la pista.

| **Medida** | **Valor** |
|---|---|
| Largo | 24 mm |
| Alto | 25 mm |
| Ancho | 12.4 mm |
| Peso | 4 g |

## Raspberry Pi AI HAT+ (26 TOPS)

<!-- github-only-start -->
<p align="center">
	Raspberry Pi AI HAT+ 26 TOPS
	<br>
	<i>Raspberry Pi AI HAT+ 26 TOPS</i>
</p>
<!-- github-only-end -->

<!-- mkdocs-only-start
<div class="hcenter">
    <img src="/assets/images/components/raspberry-pi-ai-hat-plus.png" alt="Raspberry Pi AI HAT+ 26 TOPS" 
class="component-image">
    <i>Raspberry Pi AI HAT+ 26 TOPS</i>
</div>
mkdocs-only-end -->

Si bien la Raspberry Pi 5 es capaz de procesar imágenes en tiempo real, tuvimos en cuenta que necesitaba un poco más de poder, por lo cual decidimos incorporar la AI HAT+ a la Raspberry Pi 5 para poder alcanzar el nivel de procesamiento necesario.

El Raspberry Pi AI HAT+ tiene dos versiones, una de 13 Trillones de Operaciones por Segundo (TOPS) y otra de 26 TOPS [[4](#raspberry-pi-ai-hat-documentation)]. Como se menciona en el índice, Klevor posee un Raspberry Pi AI HAT+ de 26 TOPS, gracias a este procesador de imágenes, Klevor puede analizar hasta 30 imágenes por segundo con una resolución de 640 px × 640 px.

| **Medida** | **Valor** |
|---|---|
| Largo | 65 mm |
| Alto | 5.5 mm |
| Ancho | 56 mm |
| Peso | 9.07 g |

## Raspberry Pi Pico 2 WH

<!-- github-only-start -->
<p align="center">
	Raspberry Pi Pico 2 W
	<br>
	<i>Raspberry Pi Pico 2 W</i>
</p>
<!-- github-only-end -->

<!-- mkdocs-only-start
<div class="hcenter">
    <img src="/assets/images/components/raspberry-pi-pico-2-w.png" alt="Raspberry Pi Pico 2 W" 
class="component-image">
    <i>Raspberry Pi Pico 2 W</i>
</div>
mkdocs-only-end -->

Construido sobre el chip RP2350 [[5](#raspberry-pi-pico-2-wh-datasheet)], la Raspberry Pi Pico 2 W es el microcontrolador de Klevor, además de ser un microcontrolador ligero y pequeño, este chip permite una fácil integración con el resto de los componentes Raspberry, debido a que establecer una comunicación serial con una Raspberry Pi 5 es mucho más fácil de hacer con una Raspberry Pi Pico que con algún otro microcontrolador de distinto fabricante.

Además de ofrecer una frecuencia de procesamiento de 150 Mhz, superior a varios microcontroladores de similar tamaño, como, por ejemplo, el Arduino Nano el cual cuenta con una frecuencia de procesamiento de 20 Mhz.

La versión con el módulo de WiFi integrado ofrece una gran ventaja a la hora de poder practicar, ya que nos permite ver exactamente qué está procesando Klevor en el momento, sin necesidad de utilizar, por ejemplo, LED de distintos colores para poder señalizar distintas decisiones, logrando que el producto final sea mucho más limpio.

| **Medida** | **Valor** |
|---|---|
| Largo | 51 mm |
| Alto | 12 mm |
| Ancho | 21 mm |
| Peso | 6 g |

## RPLiDAR C1

<!-- github-only-start -->
<p align="center">
	RPLiDAR C1
	<br>
	<i>RPLiDAR C1</i>
</p>
<!-- github-only-end -->

<!-- mkdocs-only-start
<div class="hcenter">
    <img src="/assets/images/components/rplidar-c1.png" alt="RPLiDAR C1" 
class="component-image">
    <i>RPLiDAR C1</i>
</div>
mkdocs-only-end -->

El RPLiDAR C1 es un escáner de rango láser de 360 grados, el cual puede detectar superficies que están hasta 12 metros de distancia, su punto ciego es de tan solo 5 centímetros alrededor del mismo [[6](#rplidar-c1-robot-shop)] | [[7](#rplidar-c1-datasheet)], todos estos factores hacen que el RPLiDAR C1 sea una gran opción para poder guíar a Klevor por la pista.

Este RPLiDAR C1 permite a Klevor poder identificar exactamente dónde está ubicado en la pista, gracias a la gran cantidad de datos que este LiDAR ofrece.

| **Medida** | **Valor** |
|---|---|
| Largo | 55.6 mm |
| Alto | 41.3 mm |
| Ancho | 55.6 mm |
| Peso | 110 g |

Especificaciones técnicas:

| **Especificación** | **Valor** |
|---|---|
| Rango de distancia | Blanco: 0,05-12 m (70 % de reflectividad); Negro: 0,05-6 m (10 % de reflectividad) |
| Frecuencia de muestreo | 5 kHz |
| Resolución angular | 0,72° |
| Ángulo de inclinación  | 0°-1,5° |

## Shargeek Storm 2

<!-- github-only-start -->
<p align="center">
	Shargeek Storm 2
	<br>
	<i>Shargeek Storm 2</i>
</p>
<!-- github-only-end -->

<!-- mkdocs-only-start
<div class="hcenter">
    <img src="/assets/images/components/shargeek-storm-2.png" alt="Shargeek Storm 2" 
class="component-image">
    <i>Shargeek Storm 2</i>
</div>
mkdocs-only-end -->

El Shargeek Storm 2 es un Power Bank, con múltiples características interesantes [[8](#shargeek-storm-2-amazon)] | [[9](#shargeek-storm-2-100w-power-bank)] como:

- 25600 mAh de almacenamiento.
- Salida ajustable de hasta 100 W.
- Pantalla integrada IPS.
- Carga de 0% a 100% en tan solo 1 hora y media.

Todos estos factores hacen que sea una opción perfecta para alimentar un controlador potente como lo es la Raspberry Pi 5.

Sin embargo, debido a su gran peso, es un componente un tanto difícil de poder incorporar

| **Medida** | **Valor** |
|---|---|
| Largo | 150.8 mm  |
| Alto | 58.9 mm |
| Ancho | 45.9 mm |
| Peso | 579 g |

## INJORA 180 Motor 48T

<!-- github-only-start -->
<p align="center">
	INJORA 180 Motor 48T
	<br>
	<i>INJORA 180 Motor 48T</i>
</p>
<!-- github-only-end -->

<!-- mkdocs-only-start
<div class="hcenter">
    <img src="/assets/images/components/injora-180-motor-48t.png" alt="INJORA 180 Motor 48T" 
class="component-image">
    <i>INJORA 180 Motor 48T</i>
</div>
mkdocs-only-end -->

El INJORA 180 Motor 48T es un motor diseñado para carros controlados por radio, ya que estos carros suelen tener un peso y medidas similares a las de Klevor, decidimos que este motor sería una buena incorporación. Debido a su tamaño compacto, bajo voltaje (necesitando apenas 7.4 V, llegamos a considerar motores de 12 V hasta, incluso de 24 V para Klevor), y bajo peso [[10](#injora-180-48t-amazon)].

A pesar de todas estas ventajas, un motor DC con capacidades de Encoder (es decir, que pueda contar sus vueltas) puede ser de mayor ventaja debido a que permite regular perfectamente los movimientos de Klevor, gracias a que, en vez de asignarle al motor que se mueva por cierto tiempo (lo cual puede hacer que, debido al más mínimo problema de rendimiento) sea susceptible a fallar, en cambio, con un motor con encoder, es mucho más sencillo debido a que, en vez de mover por tiempo, puedes mover por distancia lo que a pesar de algún problema de rendimiento, Klevor sepa perfectamente cuánta distancia recorrió, aligerando un poco la carga en la necesidad de conocer la distancia a sus alrededores

| **Medida** | **Valor** |
|---|---|
| Largo | 42.7 mm |
| Alto | 10 mm |
| Ancho | 15 mm |
| Peso | 38 g |

Especificaciones mecánicas:

| **Especificación**  | **Valor** |
|---|---|
| Velocidad sin carga | 20500rpm  |
| Corriente sin carga | 0.48A |

## INJORA MB100 20A mini ESC

<!-- github-only-start -->
<p align="center">
	INJORA MB100 20A Mini ESC
	<br>
	<i>INJORA MB100 20A Mini ESC</i>
</p>
<!-- github-only-end -->

<!-- mkdocs-only-start
<div class="hcenter">
    <img src="/assets/images/components/injora-mb100-mini-esc-20a.png" alt="INJORA MB100 20A Mini ESC" 
class="component-image">
    <i>INJORA MB100 20A Mini ESC</i>
</div>
mkdocs-only-end -->

El INJORA MB100 20A mini ESC es un controlador de velocidad electrónico [[11](#injora-mb100-r80-amazon)], normalmente (en carros RC) este se usa en conjunto con algún motor de la marca INJORA, este permite la conexión entre el INJORA 180 Motor 48T y la Raspberry Pi Pico 2.

Gracias a este dispositivo, podemos asegurar una conexión segura y efectiva entre el motor y la Pico 2, sin necesitar componentes más grandes (como un puente H L298N) para cumplir la misma función. Además que, este mini controlador de velocidad es capaz de soportar el alto amperaje (este puede superar hasta picos de 100A) que pueda consumir el motor INJORA 180.

Además de todo esto, es una parte del código bastante fácil de configurar gracias a librerías como
`adafruit_motor` que permite configurar al motor principal como un servo de rotación continua gracias al módulo
`servo`.

A su vez, gracias a que incorpora un BEC (Battery Eliminator Circuit) podemos alimentar al [INJORA 7Kg 2065 Micro Servo](#injora-7-kg-2065-micro-servo), sin necesidad de proporcionar una tercera batería o una alimentación secundaria de la misma batería.

| **Medida** | **Valor** |
|---|---|
| Largo | 37 mm |
| Alto | 22 mm |
| Ancho | 10 mm |
| Peso | 15 g |

Especificaciones mecánicas:

| **Especificación** | **Valor** |
|---|---|
| Tipo de motor compatible: | Motor Escobillado (030/050/130/**180**/370) |
| Salida BEC | 6V/3A (Modo Lineal) |

## Batería URGENEX 7.4 V

<!-- github-only-start -->
<p align="center">
	Batería URGENEX 7.4 V
	<br>
	<i>Batería URGENEX 7.4 V</i>
</p>
<!-- github-only-end -->

<!-- mkdocs-only-start
<div class="hcenter">
    <img src="/assets/images/components/urgenex-7-4v-3000mah.png" alt="Batería URGENEX 7.4 V" 
class="component-image">
    <i>Batería URGENEX 7.4 V</i>
</div>
mkdocs-only-end -->

La Batería URGENEX 7.4 V es nuestra segunda batería la cual cumple la única función de alimentar al INJORA 180 Motor 48T, además de esto es una batería recargable lo que lo convierte en una opción sólida para poder alimentar el motor principal.

Si bien cualquier batería de 7.4 V funcionaría perfectamente para poder utilizar al INJORA 180 Motor 48T, decidimos utilizar la batería URGENEX 7.4v por su alta calidad, ya que, el motor INJORA 180, en casos extremos puede llegar a consumir 100 A, lo que podría causarle problemas a la Shargeek Storm 2, por lo cual decidimos irnos por la ruta más segura y alimentar al motor con su batería propia.

Además de esto, esta batería ofrece una alta capacidad comparada con el resto del mercado, pues que esta alcanza los 3000 mAh [[12](#urgenex-3000-mah-amazon)].

| **Medida** | **Valor** |
|---|---|
| Largo | 37 mm |
| Alto | 70 mm |
| Ancho | 19 mm |
| Peso | 103 g |

## INJORA 7 kg 2065 Micro Servo

<!-- github-only-start -->
<p align="center">
	INJORA 7 kg 2065 Micro Servo
	<br>
	<i>INJORA 7 kg 2065 Micro Servo</i>
</p>
<!-- github-only-end -->

<!-- mkdocs-only-start
<div class="hcenter">
    <img src="/assets/images/components/injora-7kg-2065-micro-servo.png" alt="INJORA 7 kg 2065 Micro Servo" 
class="component-image">
    <i>INJORA 7 kg 2065 Micro Servo</i>
</div>
mkdocs-only-end -->

El INJORA 7 kg 2065 Micro Servo es el servomotor encargado de controlar la dirección de Klevor, decidimos utilizar este modelo debido a su reducido tamaño y peso, además de una precisión más que suficiente para poder manejar a Klevor. [[13](#injora-7kg-2065-amazon)].

No solo estos aspectos definieron la elección, el INJORA 7 kg 2065 ofrece también una gran precisión a pesar de su reducido tamaño, algo esencialmente vital en esta competencia.

Gracias a la librería antes mencionada, la `adafruit_motor` con el módulo
`servo`, nos permiten configurar el servo a nuestra elección, convirtiendo el uso de funciones para controlar el servo previamente establecido mucho más fácil de leer sin arriesgar el rendimiento del programa.

| **Medida** | **Valor** |
|---|---|
| Largo | 23 mm |
| Alto | 25.8 mm |
| Ancho | 13 mm |
| Peso | 20 g |

## 9-Axis IMU Gyroscope GY-BNO085

<!-- github-only-start -->
<p align="center">
	BNO085
	<br>
	<i>BNO085</i>
</p>
<!-- github-only-end -->

<!-- mkdocs-only-start
<div class="hcenter">
    <img src="/assets/images/components/bno08x.png" alt="BNO085" 
class="component-image">
    <i>BNO085</i>
</div>
mkdocs-only-end -->

El GY-BNO085 es un sensor de orientación inercial (IMU) de 9 Grados de Libertad (9DOF), ampliamente utilizado en aplicaciones que requieren un seguimiento de movimiento preciso. En el caso de Klevor, optamos por utilizar este sensor para poder lograr una mayor autonomía del robot en los cruces, ya que este sensor le permite alinearse casi perfectamente y poder ajustarse.

Además de todo esto, el poder utilizar un giroscopio le permite a Klevor contar las vueltas que ha dado tanto en el Desafío sin Obstáculos como el Desafío Cerrado de la forma más segura, ya que, a pesar de algún problema mecánico que impida que el robot sea capaz de ir completamente derecho, el giroscopio le puede hacer saber que tanto se está desvíando, siendo este uno de los componentes indispensables para poder completar este desafío.

La forma en la que lo implementamos es bastante sencilla, el giroscopio siempre está actualizando los datos de manera asíncrona cada 50 milisegundos, y Klevor maneja dos variables,
`yaw_deg` (la diferencia en grados en su orientación desde que inició en la pista hasta dónde está ubicado ahora mismo), y
`relative_yaw` la cual utiliza el mismo
`yaw_deg` para asignarse un valor, pero, en vez de reiniciarse cada vez que pasa de los -180 grados o 180 grados, simplemente le resta o suma (dependiendo del caso) 360 grados a
`relative_yaw`, luego dividimos este número entre 90, y redondeamos hacia abajo (es decir, 10.57 pasa a ser simplemente 10), y si la división es igual a -12 o 12, sabemos que ya está casi en su zona de estacionamiento y Klevor simplemente avanza un poquito y se detiene (en el caso del Desafío sin Obstáculos).

| **Medida** | **Valor** |
|---|---|
| Largo | 25.75 mm  |
| Alto | 15.5 mm |
| Ancho | 1.8 mm |
| Peso | 3 g |

# Referencias

1. *Raspberry Pi 5
   Datasheet*. (2025). Raspberry Pi Ltd. <a id="raspberry-pi-5-datasheet" href="https://datasheets.raspberrypi.com/rpi5/raspberry-pi-5-product-brief.pdf">https://datasheets.raspberrypi.com/rpi5/raspberry-pi-5-product-brief.pdf</a>

2. *Raspberry Pi camera module 3 (standard | wide |
   NOIR)*. (2025). GeekFactory. <a id="raspberry-pi-camera-module-3-geek-factory" href="https://www.geekfactory.mx/producto/raspberry-pi-camera-module-3/">https://www.geekfactory.mx/producto/raspberry-pi-camera-module-3/</a>

3. *Raspberry Pi Camera
   Documentation*. (2025). Raspberry Pi Ltd. <a id="raspberry-pi-camera-documentation" href="https://www.raspberrypi.com/documentation/accessories/camera.html">https://www.raspberrypi.com/documentation/accessories/camera.html</a>

4. *Raspberry Pi AI HAT+
   Documentation*. (2025). Raspberry Pi Ltd. <a id="raspberry-pi-ai-hat-documentation" href="https://www.raspberrypi.com/documentation/accessories/ai-hat-plus.html">https://www.raspberrypi.com/documentation/accessories/ai-hat-plus.html</a>

5. *Raspberry Pi Pico 2 WH
   Datasheet*. (2025). Raspberry Pi Ltd. <a id="raspberry-pi-pico-2-wh-datasheet" href="https://datasheets.raspberrypi.com/pico/pico-2-product-brief.pdf">https://datasheets.raspberrypi.com/pico/pico-2-product-brief.pdf</a>

6. *Escáner Láser DTOF 360° SLAMTEC RPLIDAR
   C1*. (2025). RobotShop. <a id="rplidar-c1-robot-shop" href="https://www.robotshop.com/es/products/escaner-laser-dtof-360-slamtec-rplidar-c1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">https://www.robotshop.com/es/products/escaner-laser-dtof-360-slamtec-rplidar-c1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</a>

7. *RPLidar C1 360 ToF LiDAR
   Datasheet*. (2025). RobotShop. <a id="rplidar-c1-datasheet" href="https://cdn.robotshop.com/media/R/Rpk/RB-Rpk-35/pdf/rp-lidar-360-tof-lidar-datasheet.pdf">https://cdn.robotshop.com/media/R/Rpk/RB-Rpk-35/pdf/rp-lidar-360-tof-lidar-datasheet.pdf</a>

8. *Shargeek Storm 2, banco de energía para portátil de 100 W, cargador portátil
   de 25600 mAh, primer banco de energía transparente del mundo con pantalla
   IPS, Samsung Galaxy, MacBook y
   más*. (2025). Amazon. <a id="shargeek-storm-2-amazon" href="https://www.amazon.es/Shargeek-port%C3%A1til-cargador-transparente-pantalla/dp/B09NY8GN76">https://www.amazon.es/Shargeek-port%C3%A1til-cargador-transparente-pantalla/dp/B09NY8GN76</a>

9. *Shargeek Storm 2, 100W Portable Power
   Bank*. (2025). Sharge Technology (Shenzhen) Co., Ltd. <a id="shargeek-storm-2-100w-power-bank" href="https://docs.google.com/gview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">https://docs.google.com/gview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</a>

10. *INJORA Motor Cepillado 180 48T con Piñón de Acero Inoxidable, Conector
    JST-PH2.0 para Upgrade 1/18 RC Crawler Redcat
    Ascent-18*. (2025). Amazon. <a id="injora-180-48t-amazon" href="https://www.amazon.es/INJORA-Cepillado-Inoxidable-JST-PH2-0-Ascent-18/dp/B0D97YNMLG?ref_=ast_sto_dp">https://www.amazon.es/INJORA-Cepillado-Inoxidable-JST-PH2-0-Ascent-18/dp/B0D97YNMLG?ref_=ast_sto_dp</a>

11. *INJORA MB100-R80 20A Brushed Mini ESC con Motor 180 de 48T para
    Actualización TRX4M 1/18 RC
    Crawler*. (2025). Amazon. <a id="injora-mb100-r80-amazon" href="https://www.amazon.es/INJORA-MB100-Brushed-Actualizaci%C3%B3n-Crawler/dp/B0CXT74XV6?ref_=ast_sto_dp">https://www.amazon.es/INJORA-MB100-Brushed-Actualizaci%C3%B3n-Crawler/dp/B0CXT74XV6?ref_=ast_sto_dp</a>

12. *URGENEX 3000mAh 7.4 V Li-ion Battery with Dean-Style T Plug 2S Rechargeable
    RC Battery Fit for WLtoys 4WD High Speed RC Cars and Most 1/10, 1/12, 1/16
    Scale RC Cars Trucks with 7.4V Battery
    Charger*. (2025). Amazon. <a id="urgenex-3000-mah-amazon" href="https://www.amazon.com/URGENEX-Bater%C3%ADa-enchufe-recargable-velocidad/dp/B0CYNVSN7W?ref_=ast_sto_dp">https://www.amazon.com/URGENEX-Bater%C3%ADa-enchufe-recargable-velocidad/dp/B0CYNVSN7W?ref_=ast_sto_dp</a>

13. *INJORA 7 kg 2065 Digital Servo Waterproof High Voltage Sub-Micro Shift
    Servo for TRX4 TRX6 SCX10 III 1/10 RC Crawler
    Car,1PCS*. (2025). Amazon. <a id="injora-7kg-2065-amazon" href="https://www.amazon.com/digital-impermeable-voltaje-Sub-Micro-Crawler/dp/B0BLBMVYCW?ref_=ast_sto_dp">https://www.amazon.com/digital-impermeable-voltaje-Sub-Micro-Crawler/dp/B0BLBMVYCW?ref_=ast_sto_dp</a>

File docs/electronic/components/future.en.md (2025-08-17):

# Future Components

Here is the full list with the components that we plan to use on Klevor.

## Motor 540

<!-- github-only-start -->
<p align="center">
	Motor 540
	<br>
	<i>Motor 540</i>
</p>
<!-- github-only-end -->

<!-- mkdocs-only-start
<div class="hcenter">
    <img src="/assets/images/components/motor-540.png" alt="Motor 540" 
class="component-image">
    <i>Motor 540</i>
</div>
mkdocs-only-end -->

When we talk about a "540 Motor" it usually refers to a type of DC motors, the "540" in the name, is usually referred to a size standard (usually about 36mm in diameter and 50mm in length), these are usually meant to be used on radio-controlled cars, or any other small projects, since they don't have the enough power to take onto more demanding tasks [[1](#motor-540-product-info)], now, the specific motor we want to implement (shown in the image above), meets the following specifications:

| **Measurement** | **Value** |
|---|---|
| Height | 51 mm |
| Diameter | 35 mm |
| Weight | 50 g |

Mechanical specifications:

| **Specifications**  | **Value** |
|---|---|
| No-load speed | >12000rpm |
| No-load current | >0.5A |

The main reason why we think that changing the motor would be a great option, is because by changing the power-bank to another model mentioned below, we would have a lot more weight to work with without exceeding the rules' limitations, and we wouldn't need the reduction box designed for the [INJORA 180](current.en.md#injora-180-motor-48t), which allows for a smaller and more compact chassis, since this motor has more torque than the [INJORA 180](current.en.md#injora-180-motor-48t) and Klevor wouldn't need to reduce this motor's torque a lot.

## ESC for Motors 540/550 2-3S 60 A

<!-- github-only-start -->
<p align="center">
	ESC for motores 540/550
	<br>
	<i>ESC for motores 540/550</i>
</p>
<!-- github-only-end -->

<!-- mkdocs-only-start
<div class="hcenter">
    <img src="/assets/images/components/esc-motor-540.png" alt="ESC for motores 540/550" 
class="component-image">
    <i>ESC for motores 540/550</i>
</div>
mkdocs-only-end -->

Since we plan to get a new motor for Klevor, we also need an ESC that is compatible with 540 motors since the [ESC Mini MB100](current.en.md#injora-mb100-20a-mini-esc) isn't compatible, so, if we wanted to replace the motor, we would also need to replace the ESC, however, aside from this, the ESC has some useful features, like, being able to change the use configuration by just changing the cable's position.

Physical specifications:

| **Measurement** | **Value** |
|---|---|
| Height | 20.5 mm |
| Length | 31.5 mm |
| Width | 38 mm |
| Weight | 38 g |
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

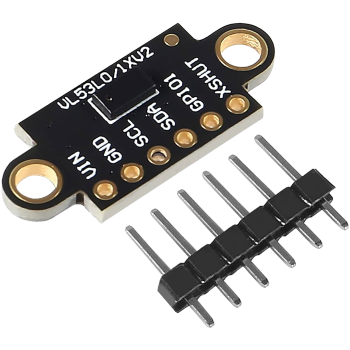
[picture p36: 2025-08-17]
docs/assets/images/components/vl53l0x.png

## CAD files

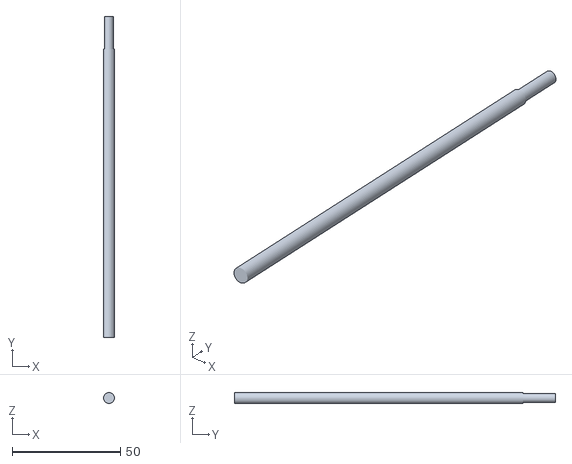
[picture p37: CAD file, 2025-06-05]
models/stl/common/current/main-transmission-shaft.stl
5.00 x 148.0 x 5.00

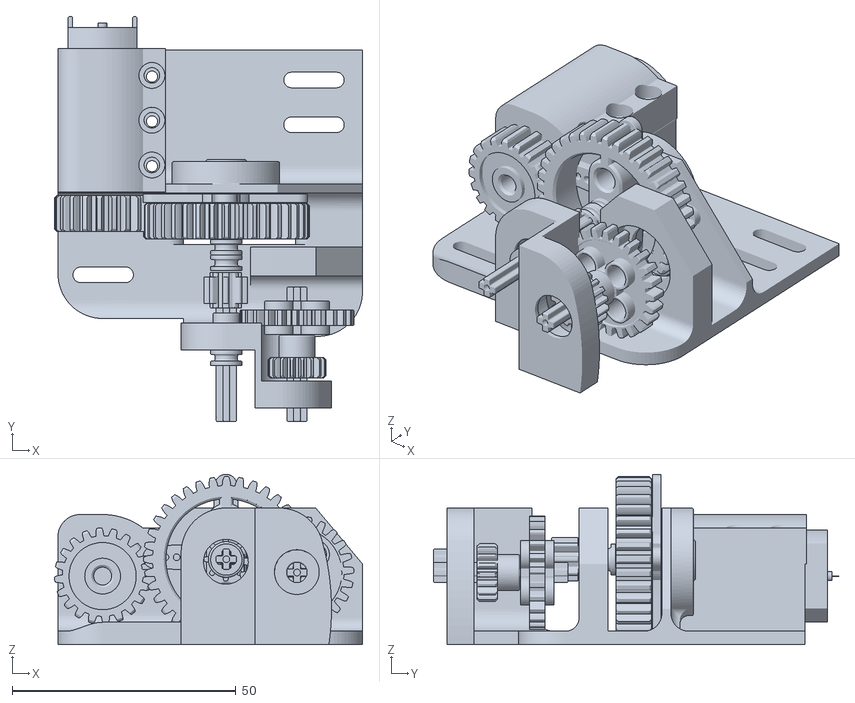
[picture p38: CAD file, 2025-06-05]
models/stl/common/current/assembled-gear-transmission.stl
68.8 x 90.4 x 38.0

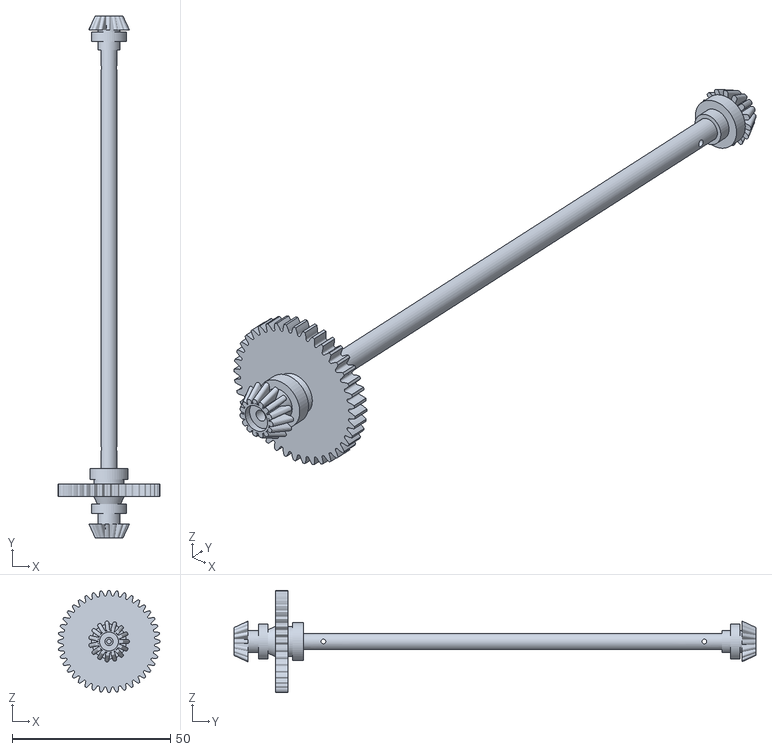
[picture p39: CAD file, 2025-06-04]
models/stl/common/current/assembled-transmission.stl
32.3 x 165.1 x 32.3

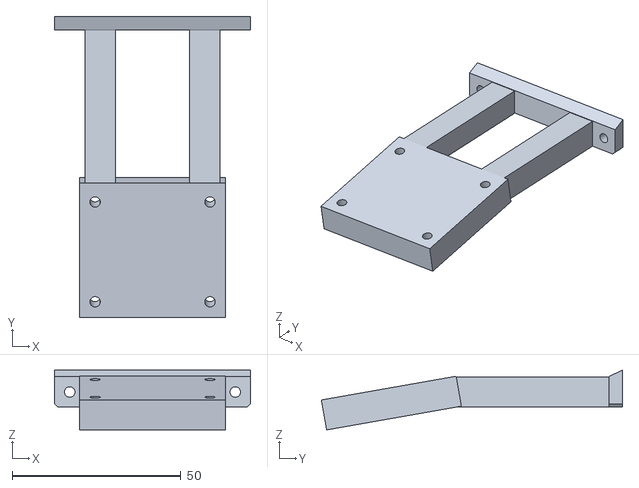
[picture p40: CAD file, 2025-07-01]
models/3d-designs/prototype2/solid-camera-mounting.stl
58.0 x 89.2 x 17.7

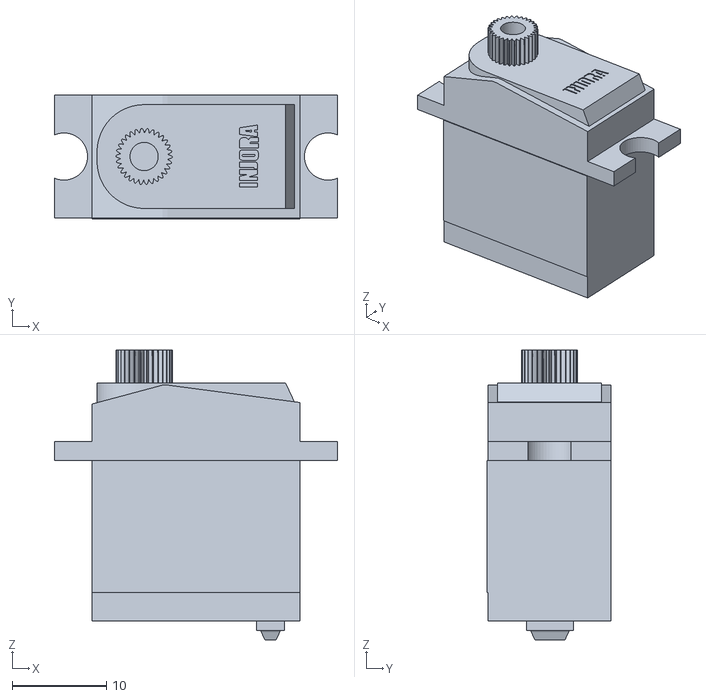
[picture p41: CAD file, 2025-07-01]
models/stl/common/current/injora-servo.stl
30.0 x 13.1 x 30.7

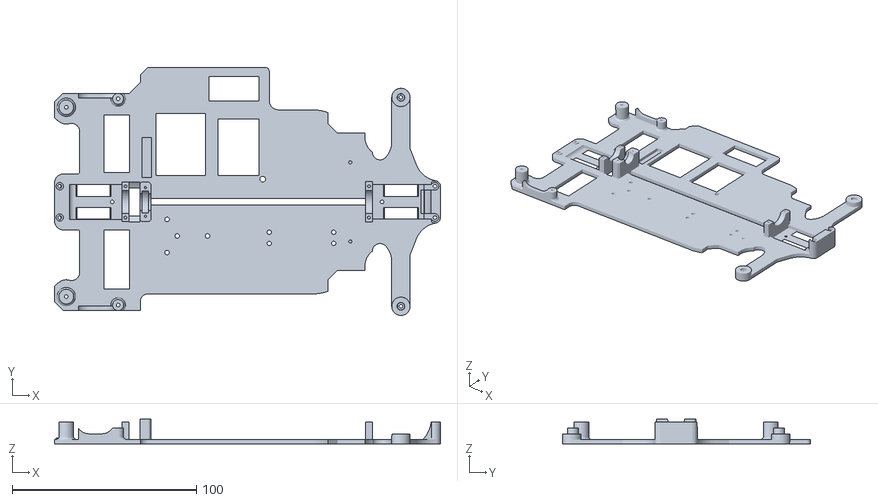
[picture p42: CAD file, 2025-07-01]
models/stl/prototype3/bottom-layer-mounting.stl
209.6 x 134.7 x 13.5

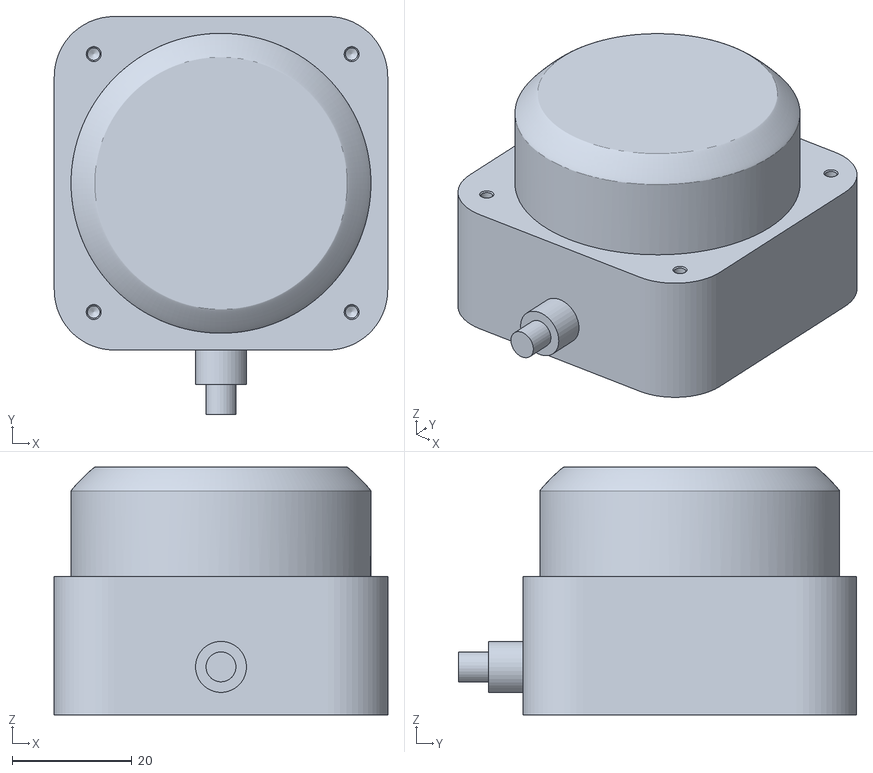
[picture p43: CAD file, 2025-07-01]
models/stl/common/current/rplidar-c1.stl
55.6 x 66.3 x 41.3

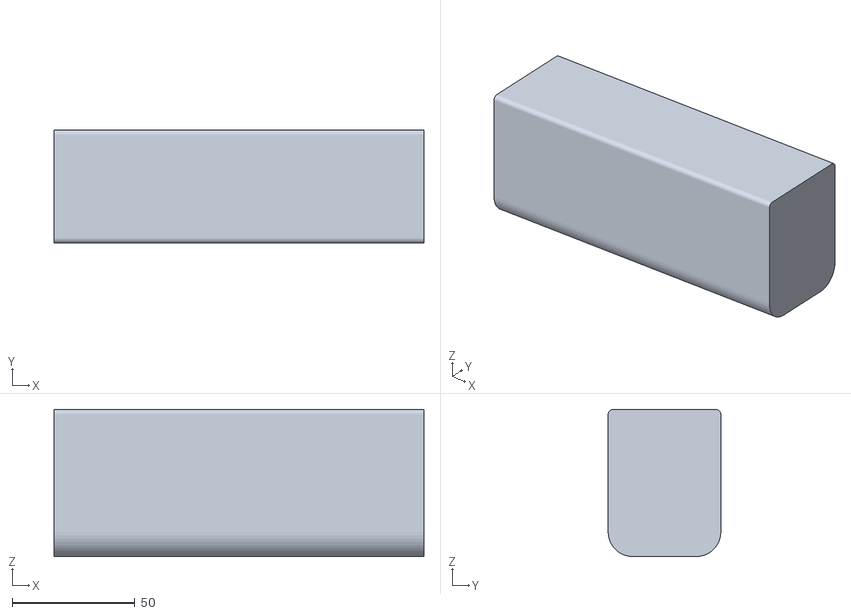
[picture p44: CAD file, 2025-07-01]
models/stl/prototype3/shargeek-storm-2.stl
151.0 x 46.0 x 60.0

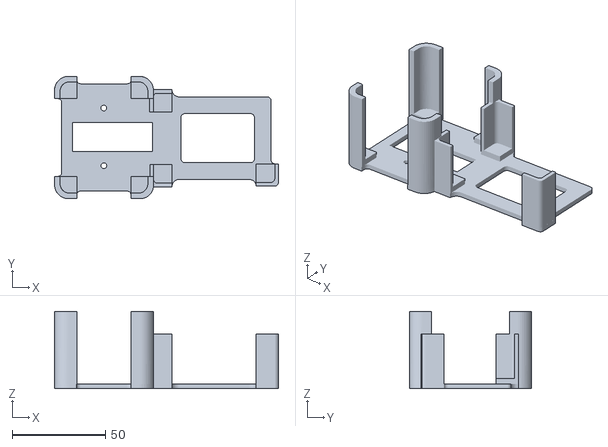
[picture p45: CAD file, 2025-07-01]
models/stl/prototype3/top-layer-mounting.stl
120.4 x 65.7 x 41.5

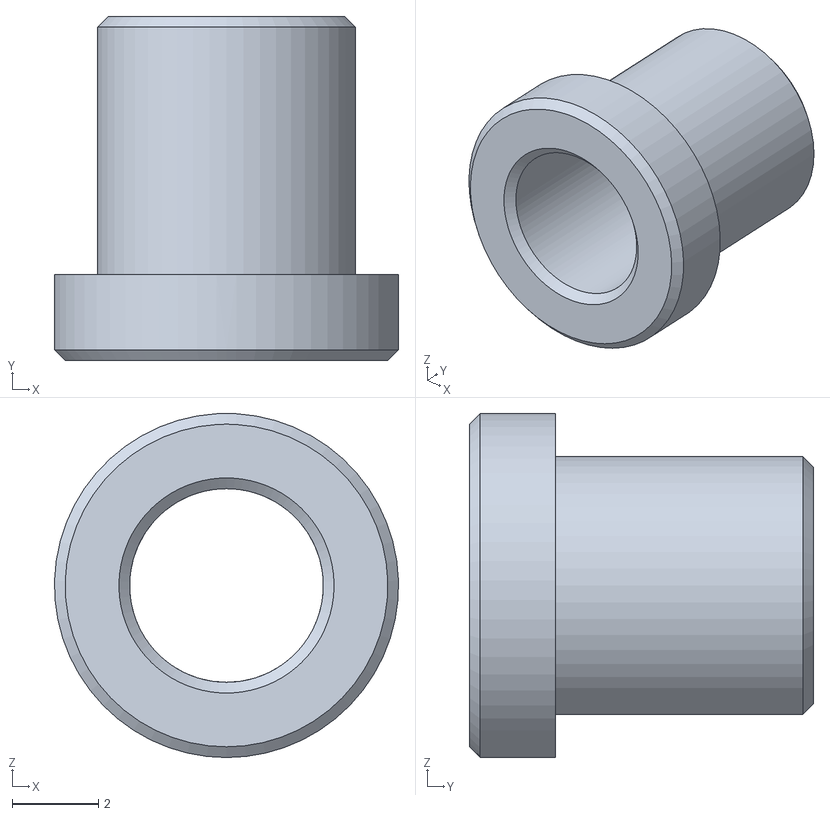
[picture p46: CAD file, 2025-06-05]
models/stl/common/current/transmission-bushing-2.stl
8.00 x 8.00 x 8.00

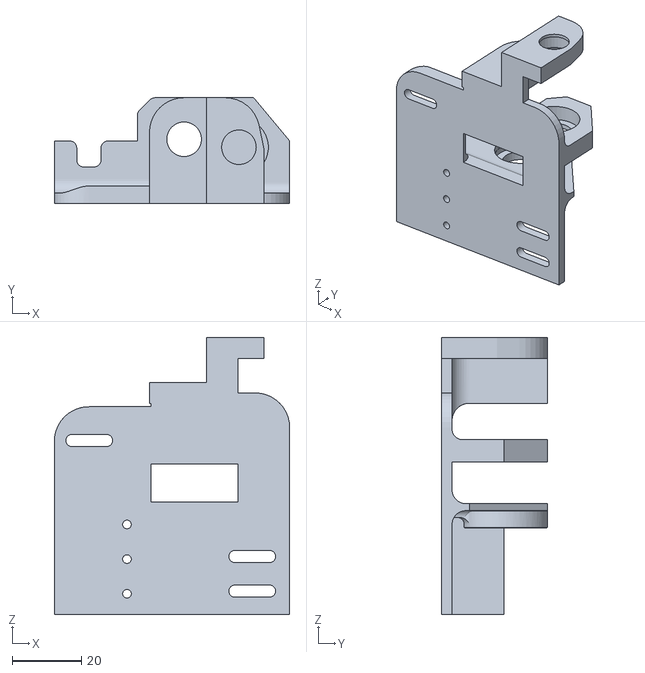
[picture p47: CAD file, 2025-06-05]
models/stl/common/current/transmission-holder.stl
68.0 x 30.5 x 80.0

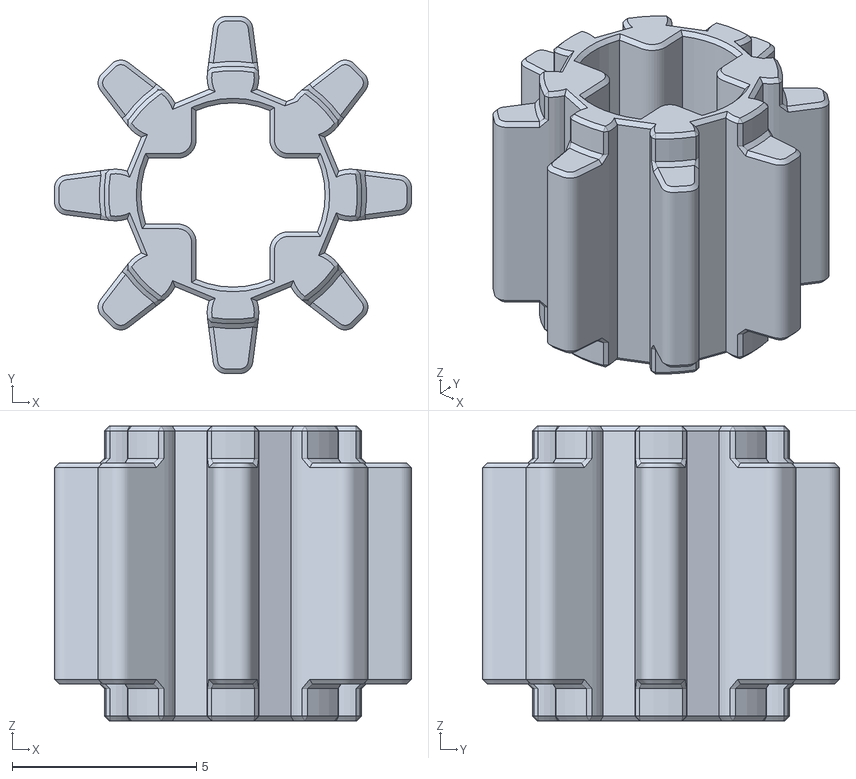
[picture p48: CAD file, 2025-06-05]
models/stl/common/current/lego-8-teeth-pinion.stl
9.69 x 9.69 x 8.00

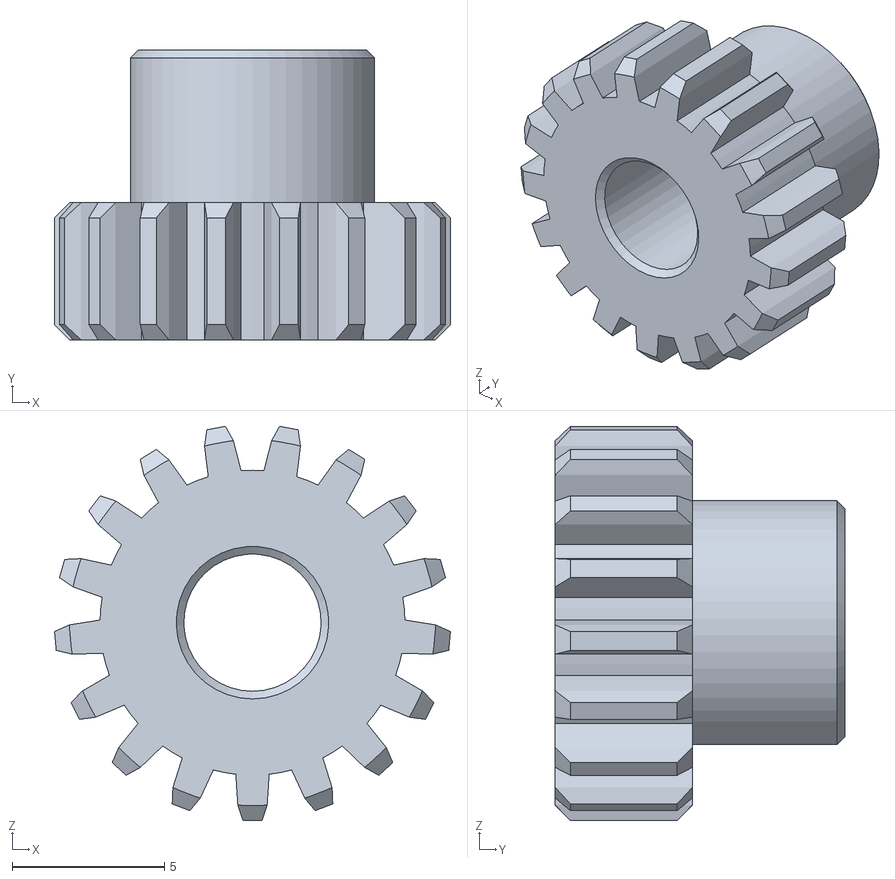
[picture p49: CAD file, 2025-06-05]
models/stl/common/current/metal-drive-pinion-17-teeth.stl
13.0 x 9.50 x 12.9

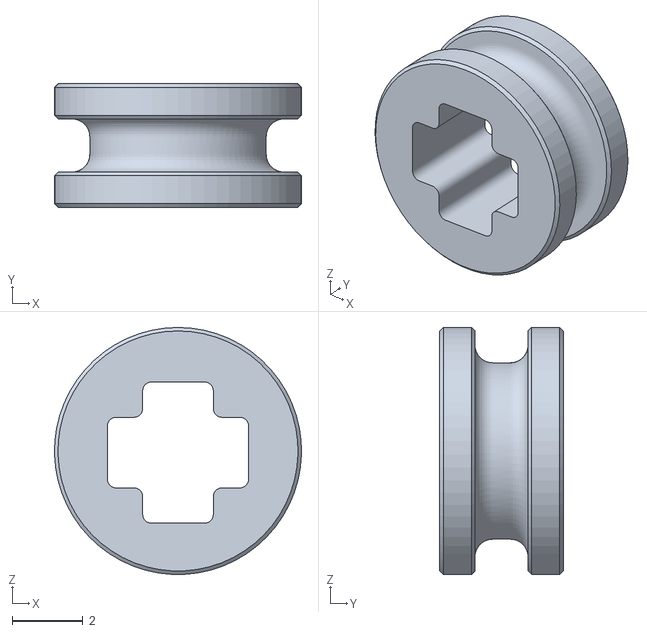
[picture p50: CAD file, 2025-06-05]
models/stl/common/current/lego-3-5-separator.stl
7.00 x 3.50 x 7.00

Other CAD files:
models/stl/common/current/servo-4-pointed-crosshead.stl
models/stl/common/current/lego-20-teeth-pinion.stl
models/stl/common/current/transmission-system-cross-bar.stl
models/stl/common/current/motor-mounting-cover.stl
models/3d-designs/prototype1/power-bank-temporary.stl
models/3d-designs/prototype1/raspberry-pi-camera-3-soporte.stl
models/3d-designs/prototype1/universal-mounting.stl
models/stl/common/current/axle-transmission.stl
models/stl/common/current/back-knuckle.stl
models/stl/common/current/big-shaft-pinion.stl
models/stl/common/current/differential.stl
models/stl/common/current/drive-shaft.stl
models/stl/common/current/front-knuckle.stl
models/stl/common/current/gearbox-bottom.stl
models/stl/common/current/gearbox-top.stl
models/stl/common/current/gyroscope.stl
models/stl/common/current/lego-24-teeth-pinion.stl
models/stl/common/current/lego-36-teeth-pinion.stl
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

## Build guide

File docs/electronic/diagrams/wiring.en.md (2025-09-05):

# Wiring Diagrams

## Version 1: Used for Prototype 1

<!-- github-only-start -->
<p align="center">
	Wiring Diagram's Version 1
	<br>
	<i>Wiring Diagram's Version 1</i>
</p>
<!-- github-only-end -->

<!-- mkdocs-only-start
<div class="hcenter">
    <img src="/assets/images/github/schemes/wiring/version1-wiring.png" alt="Wiring Diagram's Version 1" 
class="wiring-diagram-image">
    <i>Wiring Diagram's Version 1</i>
</div>
mkdocs-only-end -->

## Version 2: Used for Protypes 2 and 3

<!-- github-only-start -->
<p align="center">
	Wiring Diagram's Version 2
	<br>
	<i>Wiring Diagram's Version 2</i>
</p>
<!-- github-only-end -->

<!-- mkdocs-only-start
<div class="hcenter">
    <img src="/assets/images/github/schemes/wiring/version2-wiring.png" alt="Wiring Diagram's Version 2" 
class="wiring-diagram-image">
    <i>Wiring Diagram's Version 2</i>
</div>
mkdocs-only-end -->

## Version 3: Used for Prototype 4

<!-- github-only-start -->
<p align="center">
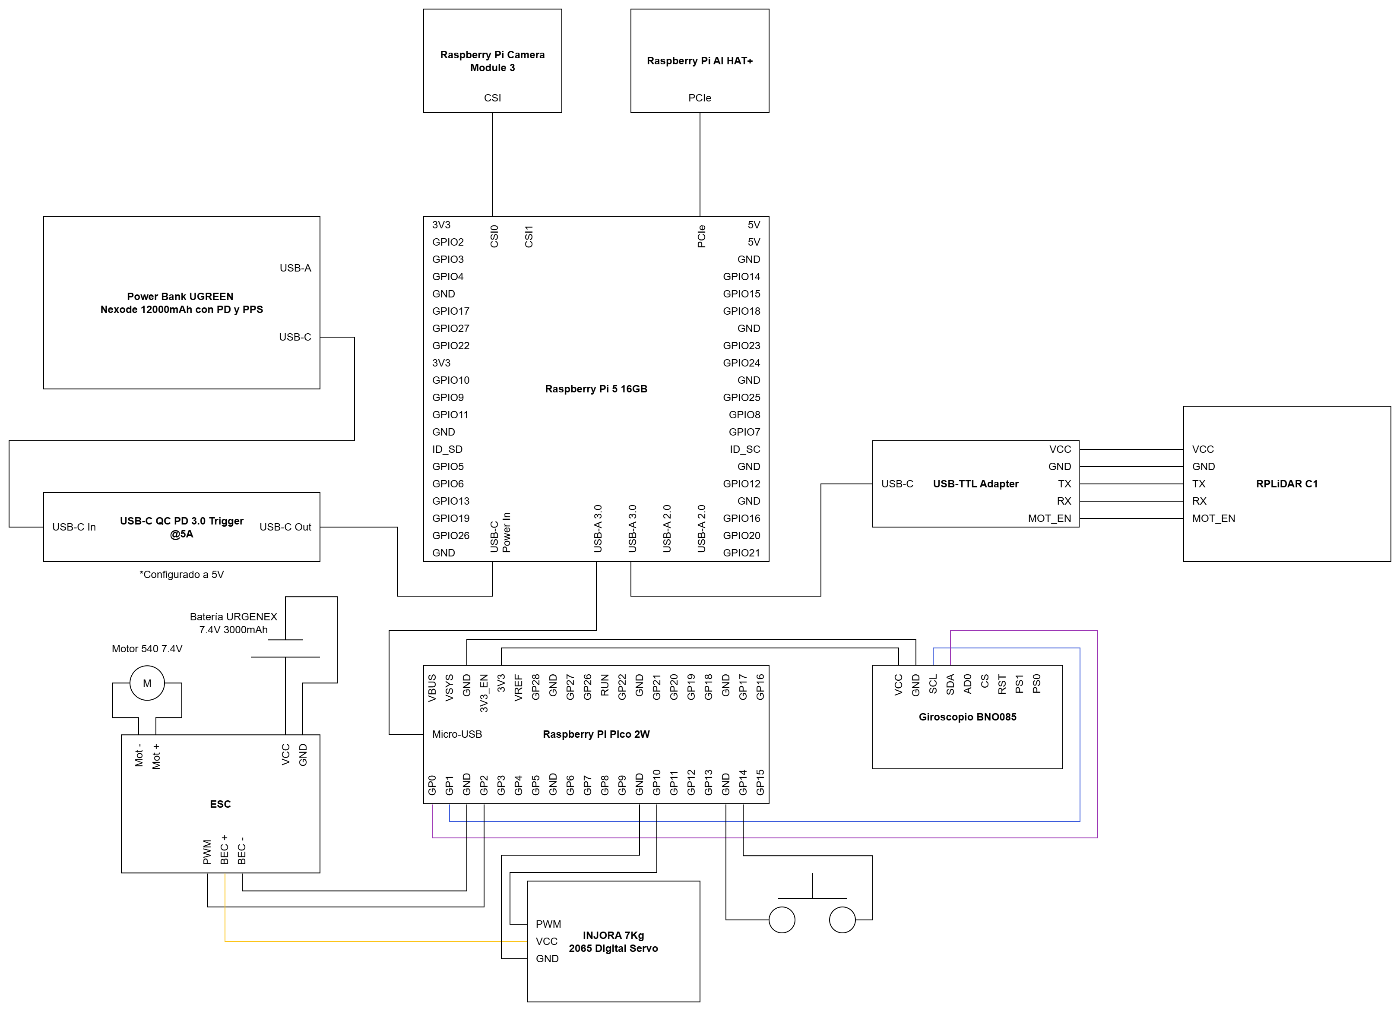
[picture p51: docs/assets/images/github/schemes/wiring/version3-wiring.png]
Wiring Diagram's Version 3
	
	<br>
	<i>Wiring Diagram's Version 3</i>
</p>
<!-- github-only-end -->

<!-- mkdocs-only-start
<div class="hcenter">
    <img src="/assets/images/github/schemes/wiring/version3-wiring.png" alt="Wiring Diagram's Version 3" 
class="wiring-diagram-image">
    <i>Wiring Diagram's Version 3</i>
</div>
mkdocs-only-end -->

## Version 4: Used for Prototype 4

<!-- github-only-start -->
<p align="center">
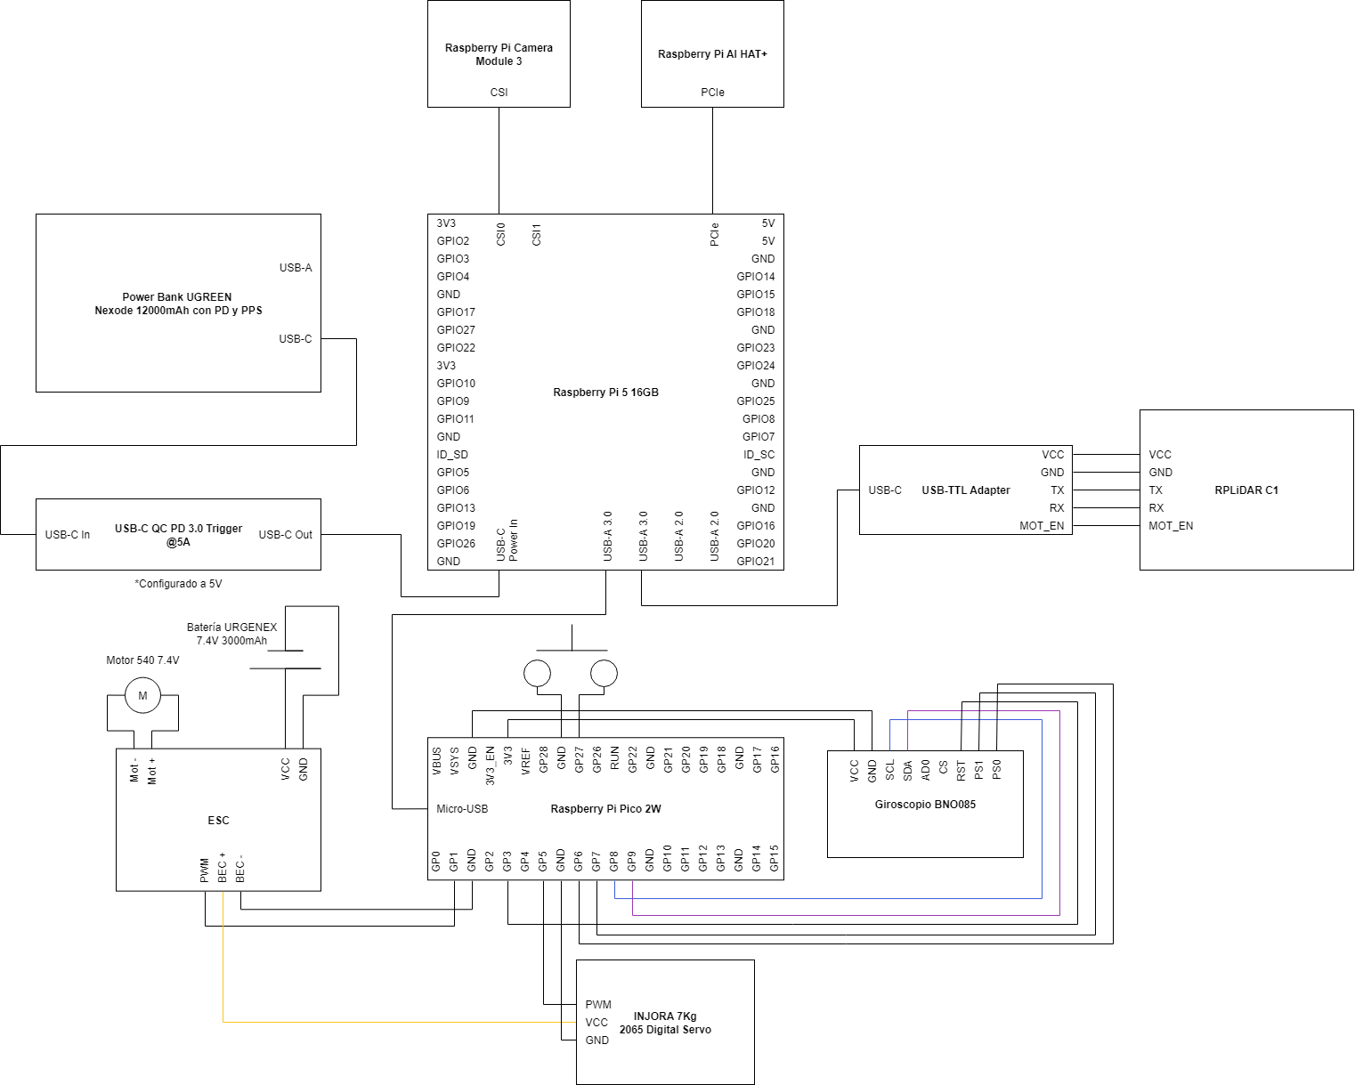
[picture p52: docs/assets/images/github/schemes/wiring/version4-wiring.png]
Wiring Diagram's Version r
	
	<br>
	<i>Wiring Diagram's Version 4</i>
</p>
<!-- github-only-end -->

<!-- mkdocs-only-start
<div class="hcenter">
    <img src="/assets/images/github/schemes/wiring/version4-wiring.png" alt="Wiring Diagram's Version 4" 
class="wiring-diagram-image">
    <i>Wiring Diagram's Version 4</i>
</div>
mkdocs-only-end -->

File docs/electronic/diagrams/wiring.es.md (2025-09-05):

# Diagramas de Conexiones

## Versión 1: Empleada en el Prototipo 1

<!-- github-only-start -->
<p align="center">
	Versión 1 del diagrama de Conexiones
	<br>
	<i>Versión 1 del diagrama de Conexiones</i>
</p>
<!-- github-only-end -->

<!-- mkdocs-only-start
<div class="hcenter">
    <img src="/assets/images/github/schemes/wiring/version1-wiring.png" alt="Versión 1 del diagrama de Conexiones" 
class="wiring-diagram-image">
    <i>Versión 1 del diagrama de Conexiones</i>
</div>
mkdocs-only-end -->

## Versión 2: Empleada en el Prototipo 2 y 3

<!-- github-only-start -->
<p align="center">
	Versión 2 del diagrama de Conexiones
	<br>
	<i>Versión 2 del diagrama de Conexiones</i>
</p>
<!-- github-only-end -->

<!-- mkdocs-only-start
<div class="hcenter">
    <img src="/assets/images/github/schemes/wiring/version2-wiring.png" alt="Versión 2 del diagrama de Conexiones" 
class="wiring-diagram-image">
    <i>Versión 2 del diagrama de Conexiones</i>
</div>
mkdocs-only-end -->

## Versión 3: Empleada en el Prototipo 4

<!-- github-only-start -->
<p align="center">
	Versión 3 del diagrama de Conexiones
	<br>
	<i>Versión 3 del diagrama de Conexiones</i>
</p>
<!-- github-only-end -->

<!-- mkdocs-only-start
<div class="hcenter">
    <img src="/assets/images/github/schemes/wiring/version3-wiring.png" alt="Versión 3 del diagrama de Conexiones" 
class="wiring-diagram-image">
    <i>Versión 3 del diagrama de Conexiones</i>
</div>
mkdocs-only-end -->

## Versión 4: Empleada en el Prototipo 4

<!-- github-only-start -->
<p align="center">
	Versión 4 del diagrama de Conexiones
	<br>
	<i>Versión 4 del diagrama de Conexiones</i>
</p>
<!-- github-only-end -->

<!-- mkdocs-only-start
<div class="hcenter">
    <img src="/assets/images/github/schemes/wiring/version4-wiring.png" alt="Versión 4 del diagrama de Conexiones" 
class="wiring-diagram-image">
    <i>Versión 4 del diagrama de Conexiones</i>
</div>
mkdocs-only-end -->

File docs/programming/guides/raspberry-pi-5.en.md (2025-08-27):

# Raspberry Pi 5 Guide

## Raspberry Pi OS installation

<!-- github-only-start -->
<p align="center">
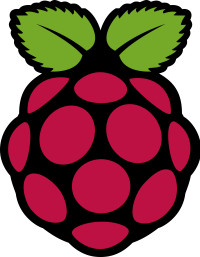
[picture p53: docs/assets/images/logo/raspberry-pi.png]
Raspberry Pi's Logo
    
    <br>
    <i>Raspberry Pi's Logo</i>
</p>
<!-- github-only-end -->

<!-- mkdocs-only-start
<div class="hcenter">
    <img src="/assets/images/logo/raspberry-pi.png" alt="Raspberry Pi's Logo" 
class="logo--3rd-party">
    <i>Raspberry Pi's Logo</i>
</div>
mkdocs-only-end -->

Raspberry Pi OS is the official operatving system for the Raspberry Pi series, based on Debian Linux, and is widely used for programming and robotics projects due to its ease of use and its wide support [[1](#raspberry-pi-os)]. Next, we detail the steps needed to install it in a Raspberry Pi:

1. Download the Raspberry Pi OS image from the official site [Raspberry Pi OS](https://www.raspberrypi.com/software/).
2. Copy the image and paste it into a microSD card using a software like Balena Etcher or Raspberry Pi Imager.
3. Insert the microSD card into the Raspberry Pi and turn it on.
4. Configure the Raspberry Pi following the on-screen instruction, including connecting to a Wi-Fi network and the account creation.
5. Update the operating system running the following commands in the terminal:
   ```bash 
   sudo apt update
   sudo apt upgrade
   ```

<!-- github-only-start -->
<p align="center">
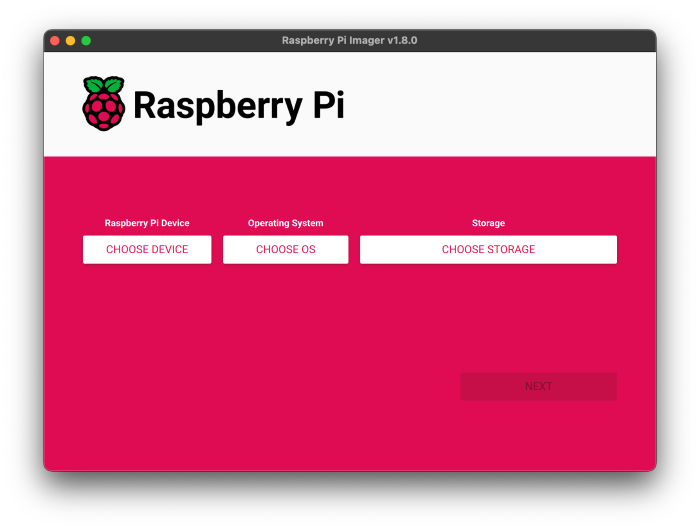
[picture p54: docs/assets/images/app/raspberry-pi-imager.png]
Raspberry Pi Imager
    
    <br>
    <i>Raspberry Pi Imager</i>
</p>

<!-- github-only-end -->

<!-- mkdocs-only-start
<div class="hcenter">
    <img src="/assets/images/app/raspberry-pi-imager.png" alt="Raspberry Pi Imager" class="app--image">
    <i>Raspberry Pi Imager</i>
</div>
mkdocs-only-end -->

> [!IMPORTANT]
> Due to personal experience, we recommend configuring the official application from Raspberry Pi for remote connection, Raspberry Pi Connect, which allows to access the Raspberry Pi anywhere without the need to be connected in the same wifi network [[2](#raspberry-pi-connect)]. In our case, it allowed us multiple times, remotely, through the Remote Shell mode, to kill processes that have resulted in crashed or have limited the response time from the Raspberry Pi.

## Camera Installation

<!-- github-only-start -->
<p align="center">
    Raspberry Pi Camera Module 3
    <br>
    <i>Raspberry Pi Camera Module 3</i>
</p>
<!-- github-only-end -->

<!-- mkdocs-only-start
<div class="hcenter">
    <img src="/assets/images/components/raspberry-pi-camera-module-3.png" alt="Raspberry Pi Camera Module 3" 
class="component-image">
    <i>Raspberry Pi Camera Module 3</i>
</div>
mkdocs-only-end -->

To install the camera in the Raspberry Pi, it is needed to follow these steps. It is worth mentioned that the camera used in this project is the [Raspberry Pi Camera Module 3 Wide](../../electronic/components/current.en.md#raspberry-pi-camera-module-3-wide), which is compatible with the Raspberry pi 5 and allows to capture high-quality images and videos [[3](#camera-docs)].

1. Connect the camera to the Raspberry Pi using the CSI connector.
2. Check the proper working of the camera by running the following command in the terminal:
   ```bash
   libcamera-hello
   ```
3. If the camera works correctly, a preview of the camera will be shown on screen for a few seconds.

> [!IMPORTANT]
> In case you are interested in acquiring any of the Raspberry Pi Camera, it's needed to buy a separate cable depending on the supplier, normally, these cameras come with the Raspberry Pi 4 cable, which is incompatible with the Raspberry Pi 5.

## Raspberry Pi AI HAT+ Installation

<!-- github-only-start -->
<p align="center">
    Raspberry Pi AI HAT+ 26 TOPS
    <br>
    <i>Raspberry Pi AI HAT+ 26 TOPS</i>
</p>
<!-- github-only-end -->

<!-- mkdocs-only-start
<div class="hcenter">
    <img src="/assets/images/components/raspberry-pi-ai-hat-plus.png" alt="Raspberry Pi AI HAT+ 26 TOPS" 
class="component-image">
    <i>Raspberry Pi AI HAT+ 26 TOPS</i>
</div>
mkdocs-only-end -->

To install it, we used both guides from the Raspberry Pi official documentation, where it is explained how to install the Hailo AI HAT+ [[4](#getting-started-raspberry-pi)] and how to install the software required for its operation [[5](#ai-hat-plus-raspberry-pi)].

1. Check the Raspberry Pi 5 is up-to-date, if not, update it with the following command:
    ```bash
    sudo apt update && sudo apt full-upgade
    ```
2. Check the installed firmware version with the following command:
    ```bash
    sudo rpi-eeprom-update
    ```
    1. If said command returns a date earlier than December 6th, 2023, its needed to update the Raspberry Pi 5's firmware. To do this, we run the following command:
        ```bash
        sudo raspi-config
        ```
    2. In the configuration menu, select the option `Advanced Options` and then `Bootloader Version`. Choose the option `Latest` and exit the configuration menu.
3. Execute the following command to update the firmware:
    ```bash
    sudo rpi-eeprom-update -a
    ```
4. Reboot the Raspberry Pi 5 with the following command:
    ```bash
    sudo reboot
    ```
5. Unplug the Raspberry Pi 5 and disconnect all the devices connected to it.
6. Install the spacers on the Raspberry Pi 5 using the four screws provided. Press firmly the GPIO connecter stacked over the Raspberry Pi GPIO connector. Disconnect the flat cable from the AI HAT+ and connect the other end to the Raspberry Pi's PCIe port. Lift the flat cable's support from both sides, then insert the cable with the copper contact point inside, to the USB ports. With the flat cable completely inserted in the PCIe port, push the cable's support down from both sides to lock the flat cable firmly in its place.
7. Put the AI HAT+ over the spacers and use the four screws remaining to lock it in its place.
8. Connect the flat cable to the AI HAT+ and secure it. To do so, lift the flat cable's support from both sides, then insert the cable with the copper contact point inside, to the USB ports. With the flat cable completely inserted in the PCIe port, push the cable's support down from both sides to lock the flat cable firmly in its place.
9. Plug the Raspberry pi 5 back in and turn on the device.
10. To enable PCIe Gen 3.0 speeds [[6](#computers-raspberry-pi)], run the following command:
    ```bash
    sudo raspi-config
    ```
    1. In the settings menu, select the option `Advanced Options` and then `PCIe Speed`. Choose the option `Yes` to enable PCIe Gen 3.0 mode.
    2. Reboot the Raspberry Pi 5.
11. Install the dependencies required to use the NPU. Run the following command from a window in a terminal.
    ```bash
    sudo apt install hailo-all
    ```
    It is worth noting that, because the latest version (4.21.0) was very recent at the time, we recommend using the 4.20.0 version, since we worked and tested its proper functioning on this version, to do so, instead of running the previous command, run:
    ```bash
    sudo apt install hailo-all=4.20.0
    ```
    This will install the following dependencies:
    - Hailo kernel device driver and firmware
    - HailoRT middleware software
    - Hailo Tappas Core Post-Processing Libraries
    - Hailo rpicam-apps post-processing demo software stages
12. Finally, reset the Raspberry Pi again so these changes take effect
13. To check the NPU is properly installed and working, run the following command:
    ```bash
    hailortcli fw-control identify
    ```
    If the NPU is installed correctly, you should see a message similar to this:
    ```bash
    Executing on device: 0001:01:00.0
    Identifying board
    Control Protocol Version: 2
    Firmware Version: 4.20.0 (release,app,extended context switch buffer)
    Logger Version: 0
    Board Name: Hailo-8
    Device Architecture: HAILO8
    Serial Number: <N/A>
    Part Number: <N/A>
    Product Name: <N/A>
    ```

## Raspberry Pi Configuration

<!-- github-only-start -->
<p align="center">
    Raspberry Pi 5
    <br>
    <i>Raspberry Pi 5</i>
</p>
<!-- github-only-end -->

<!-- mkdocs-only-start
<div class="hcenter">
    <img src="/assets/images/components/raspberry-pi-5.png" alt="Raspberry Pi 5" 
class="component-image">
    <i>Raspberry Pi 5</i>
</div>
mkdocs-only-end -->

To configure the Raspberry Pi, first connect the Raspberry Pi to a monitor, mouse and keyboard.

Then, turn on the Raspberry Pi and wait until the operating system starts.

After, open a terminal and execute the following command to update the operating system:

```bash
sudo apt update && sudo apt upgrade -y
```

Clone the repository in case you haven't done so. You can see the multiple ways of cloning the repository in this section [GitHub](../../github.en.md#repository).

Navegate to the cloned repository's directory, in case its cloned in the Documents folder, the command would be:

```bash
cd ~/Documents/klevor
```

Change the current directory to `devices/raspberry_pi_5` to access the code used for the Raspberry Pi 5:

```bash
cd devices/raspberry_pi_5
```
Configure Python's virtual environment. To do so, run the following command:

- If the operating system is Windows:
    ```cmd
    python -m venv .venv
    .\.venv\Scripts\activate
    ```
- If the operating system is Linux or macOS:
    ```bash
    python3 -m venv .venv
    source .venv/bin/activate
    ```

Install the required dependencias for the project running the following command:

```bash
pip install -r requirements.txt
```

In case the Raspberry Pi Pico 2 W isn't configured, it is recommended to follow its respective [Configuration Guide](raspberry-pi-pico-2w.en.md#configuration) to be able to use it as the robot's controller. In the same way as, if the object detection model isn't generated yet, it is recommended to follow the [Model Creation Guide](object-detection.en.md) to be able to use it with the Raspberry Pi 5.

### Configure the Startup Service

To be able to make sure the robot starts automatically by just turning the Raspberry Pi on, its required to configure a Startup Service

To do so, first check the Shell script `run.sh` is executable, to which, run the following command:

```bash
chmod +x run.sh
```

> [!NOTE]
> You need to be inside of the `devices/raspberry_pi_5` directory so the previous command works.

After, we create a service file inside the directory `/etc/systemd/system` with the name `klevor.service` with the following command:

```bash
sudo nano /etc/systemd/system/klevor.service
```
In the text editor, paste the following command:

```ini
[Unit]
Description=Klevor Startup Service
After=multi-user.target

[Service]
User=pi
ExecStart=/home/pi/Documents/klevor/devices/raspberry_pi_5/run.sh
WorkingDirectory=/home/pi/Documents/klevor/devices/raspberry_pi_5
StandardOutput=inherit
StandardError=inherit
Restart=on-failure

[Install]
WantedBy=multi-user.target
```

> [!NOTE]
> Replace `user` with the user name in the Raspberry Pi, which by default is `pi`. Also, replace `/home/pi/Documents/klevor/devices/raspberry_pi_5/run.sh` with the complete route to the script `run.sh` which is located inside of the cloned repository's directory. Also, adjust the route from the `WorkingDirectory` with the location of the `run.sh` script directory is located in.

Save the changes and exit the text editor (in nano, press `Ctrl+X`, and then `Y` to confirm the chagnes, and finally `Enter`).

Then, reload the system's services with the following command:

```bash
sudo systemctl daemon-reload
```

Finally, enable the service to start automatically whenever the Raspberry Pi starts with the following command:

```bash
sudo systemctl enable klevor.service
```

> [!NOTE]
> If you need to stop the service, you can do so with the following command:
> ```bash
> sudo systemctl stop klevor.service	
> ```

Reboot the Raspberry Pi to make the changes take effect. From now on, the robot will start automatically whenever the Raspberry Pi is turned on.

> [!IMPORTANT]
> Due to the code's logic, the robot will not move until a button or switch is pressed, as it is shown on the robot's connections diagram. This is to prevent the robot accidentally moving after turning on the Raspberry Pi. You can view the connecting diagram in the [Electronics](../../electronic/diagrams/  wiring.en.md) section.

> [!IMPORTANT]
> If you think the robot did not start correctly, you can check the service's status with the following command:
> ```bash
> sudo systemctl status klevor.service
> ```
> Also, you can execute the code directly without configuring the startup service, to do so, simply run the following command:
> ```bash
> run.sh
> ```
> This will start the robot and it will start to print the debugging messages in the terminal. If everything works correctly, you should see messages indicating that the robot is ready to receive commands.
> If you wish to stop the robot, you can press `Ctrl + C` in the terminal where the script `run.sh` is being run on.

# References

1. *Raspberry Pi OS*. (2025). Raspberry Pi. <a id="raspberry-pi-os" href="https://www.raspberrypi.com/software/">https://www.raspberrypi.com/software/</a>

2. *Raspberry Pi Connect*. (2025). Raspberry Pi. <a id="raspberry-pi-connect" href="https://www.raspberrypi.com/documentation/remote-access/raspberry-pi-connect.html">https://www.raspberrypi.com/documentation/remote-access/raspberry-pi-connect.html</a>

3. *Camera*. (2025). Raspberry Pi. <a id="camera-docs" href="https://www.raspberrypi.com/documentation/computers/camera.html">https://www.raspberrypi.com/documentation/computers/camera.html</a>

4. *AI Kit and AI HAT+ software*. (2025). Raspberry Pi. <a id="getting-started-raspberry-pi" href="https://www.raspberrypi.com/documentation/computers/ai.html#getting-started">https://www.raspberrypi.com/documentation/computers/ai.html#getting-started</a>

5. *AI Hat+*. (2025). Raspberry Pi. <a id="ai-hat-plus-raspberry-pi" href="https://www.raspberrypi.com/documentation/accessories/ai-hat-plus.html#ai-hat-plus">https://www.raspberrypi.com/documentation/accessories/ai-hat-plus.html#ai-hat-plus</a>

6. *Raspberry Pi*. (2025). Raspberry Pi. <a id="computers-raspberry-pi" href="https://www.raspberrypi.com/documentation/computers/raspberry-pi.html">https://www.raspberrypi.com/documentation/computers/raspberry-pi.html</a>

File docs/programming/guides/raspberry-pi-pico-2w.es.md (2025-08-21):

# Guía de la Raspberry Pi Pico 2 W

*En Desarrollo*

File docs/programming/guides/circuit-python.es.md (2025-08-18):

# Guía de CircuitPython

## Instalación de CircuitPython

<!-- github-only-start -->
<p align="center">
	Logo de CircuitPython
	<br>
	<i>Logo de CircuitPython</i>
</p>
<!-- github-only-end -->

<!-- mkdocs-only-start
<div class="hcenter">
    <img src="/assets/images/logo/circuit-python.png" alt="Logo de CircuitPython" 
class="logo--3rd-party">
    <i>Logo de CircuitPython</i>
</div>
mkdocs-only-end -->

El proceso para instalar CircuitPython es prácticamente el mismo método que se usa para poder instalar MicroPython, en resumidas cuentas lo que hay que hacer es:

1. Descargar la última versión de CircuitPython para Raspberry Pi Pico desde el sitio oficial: [CircuitPython](https://circuitpython.org/board/raspberry_pi_pico2_w/).
2. Presionar el botón BOOTSEL en la Raspberry Pi Pico 2 WH y conectarla a la computadora mediante un cable USB (mantener presionado el botón hasta que se reconozca la Pico como un dispositivo de almacenamiento).
3. Copiar el archivo `.uf2` descargado en la unidad de almacenamiento de la Raspberry Pi Pico. Automáticamente, la Raspberry Pi Pico se reiniciará.
4. Desconectar la Raspberry Pi Pico y volver a conectarla sin presionar el botón BOOTSEL

Después del reinicio, tu Raspberry Pi Pico debería aparecer ahora como una nueva unidad de disco llamada "CIRCUITPY" además de tener unos archivos como `code.py` [[1](#circuit-python-docs)]. Esto significa que la instalación fue exitosa y CircuitPython está listo para usar.

# Referencias

1. *CircuitPython*. (2025). CircuitPython. <a id="circuit-python-docs" href="https://docs.circuitpython.org/en/latest/README.html">https://docs.circuitpython.org/en/latest/README.html</a>

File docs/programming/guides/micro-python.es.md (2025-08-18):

# Guía de MicroPython

## Instalación de MicroPython

<!-- github-only-start -->
<p align="center">
	Logo de MicroPython
	<br>
	<i>Logo de MicroPython</i>
</p>
<!-- github-only-end -->

<!-- mkdocs-only-start
<div class="hcenter">
    <img src="/assets/images/logo/micro-python.png" alt="Logo de MicroPython" 
class="logo--3rd-party">
    <i>Logo de MicroPython</i>
</div>
mkdocs-only-end -->

Por defecto, la Raspberry Pi Pico 2 WH viene con MicroPython preinstalado. Sin embargo, si deseas instalar una versión diferente o actualizarla, puedes seguir estos pasos [[1](#micro-python-docs)] | [[2](#raspberry-pi-micro-python-docs)]:

1. Descargar la última versión de MicroPython para Raspberry Pi Pico desde el sitio oficial: [MicroPython](https://micropython.org/download/rp2-pico-w/).
2. Presionar el botón BOOTSEL en la Raspberry Pi Pico 2 WH y conectarla a la computadora mediante un cable USB (mantener presionado el botón hasta que se reconozca la Pico como un dispositivo de almacenamiento).
3. Copiar el archivo `.uf2` descargado en la unidad de almacenamiento de la Raspberry Pi Pico. Automáticamente, la Raspberry Pi Pico se reiniciará.
4. Desconectar la Raspberry Pi Pico y volver a conectarla sin presionar el botón BOOTSEL.

# Referencias

1. *MicroPython*. (2025). MicroPython. <a id="micro-python-docs" href="https://micropython.org/">https://micropython.org/</a>

2. *MicroPython*. (2025). Raspberry Pi. <a id="raspberry-pi-micro-python-docs" href="https://www.raspberrypi.com/documentation/micropython/">https://www.raspberrypi.com/documentation/micropython/</a>

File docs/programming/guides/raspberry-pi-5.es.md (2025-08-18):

# Guía de la Raspberry Pi 5

## Instalación de Raspberry Pi OS

<!-- github-only-start -->
<p align="center">
	Logo de Raspberry Pi
	<br>
	<i>Logo de Raspberry Pi</i>
</p>
<!-- github-only-end -->

<!-- mkdocs-only-start
<div class="hcenter">
    <img src="/assets/images/logo/raspberry-pi.png" alt="Logo de Raspberry Pi" 
class="logo--3rd-party">
    <i>Logo de Raspberry Pi</i>
</div>
mkdocs-only-end -->

Raspberry Pi OS es el sistema operativo oficial para las Raspberry Pi, basado en Debian Linux, y es ampliamente utilizado para proyectos de programación y robótica debido a su facilidad de uso y amplia comunidad de soporte [[1](#raspberry-pi-os)]. A continuación, se detallan los pasos para instalarlo en una Raspberry Pi:

1. Descargar la imagen de Raspberry Pi OS desde el sitio oficial: [Raspberry Pi OS](https://www.raspberrypi.com/software/).
2. Grabar la imagen en una tarjeta microSD utilizando un software como Balena Etcher o Raspberry Pi Imager.
3. Insertar la tarjeta microSD en la Raspberry Pi y encenderla.
4. Configurar la Raspberry Pi siguiendo las instrucciones en pantalla, incluyendo la conexión a una red wifi y la creación de un usuario.
5. Actualizar el sistema operativo ejecutando los siguientes comandos en la terminal:
   ```bash 
   sudo apt update
   sudo apt upgrade
   ```

<!-- github-only-start -->
<p align="center">
	Raspberry Pi Imager
	<br>
	<i>Raspberry Pi Imager</i>
</p>

<!-- github-only-end -->

<!-- mkdocs-only-start
<div class="hcenter">
    <img src="/assets/images/app/raspberry-pi-imager.png" alt="Raspberry Pi Imager" class="app--image">
    <i>Raspberry Pi Imager</i>
</div>
mkdocs-only-end -->

> [!IMPORTANT]
> Por experiencia propia, recomendamos la configuración de la aplicación oficial de Raspberry Pi para conexión remota, Raspberry Pi Connect, que permite acceder a la Raspberry Pi desde cualquier lugar y sin necesidad de estar conectado a la misma red wifi [[2](#raspberry-pi-connect)]. En nuestro caso, en reiteradas ocasiones nos permitió de forma remota, a través del modo Remote Shell, eliminar procesos que han producido un crash o han limitado la repuesta de la Raspberry Pi.

## Instalación de la Cámara

<!-- github-only-start -->
<p align="center">
	Raspberry Pi Camera Module 3
	<br>
	<i>Raspberry Pi Camera Module 3</i>
</p>
<!-- github-only-end -->

<!-- mkdocs-only-start
<div class="hcenter">
    <img src="/assets/images/components/raspberry-pi-camera-module-3.png" alt="Raspberry Pi Camera Module 3" 
class="component-image">
    <i>Raspberry Pi Camera Module 3</i>
</div>
mkdocs-only-end -->

Para instalar la cámara en la Raspberry Pi, se debe seguir los siguientes pasos. Cabe destacar que la cámara utilizada en este proyecto es la [Raspberry Pi Camera Module 3 Wide](../../electronic/components/current.es.md#raspberry-pi-camera-module-3-wide), que es compatible con la Raspberry Pi 5 y permite capturar imágenes y videos de alta calidad [[3](#camera-docs)].

1. Conectar la cámara a la Raspberry Pi utilizando el conector CSI.
2. Probar el correcto funcionamiento de la cámara ejecutando el siguiente comando en la terminal:
   ```bash
   libcamera-hello
   ```
3. Si la cámara funciona correctamente, se mostrará una vista previa de la cámara en la pantalla por unos segundos.

> [!IMPORTANT]
> En caso de estar interesado en adquirir algún tipo de Raspberry Pi Camera, se debe comprar un cable aparte dependiendo del proveedor, ya que normalmente estas vienen con el cable para la Raspberry Pi 4, el cual no es el mismo.

## Instalación de Raspberry Pi AI HAT+

<!-- github-only-start -->
<p align="center">
	Raspberry Pi AI HAT+ 26 TOPS
	<br>
	<i>Raspberry Pi AI HAT+ 26 TOPS</i>
</p>
<!-- github-only-end -->

<!-- mkdocs-only-start
<div class="hcenter">
    <img src="/assets/images/components/raspberry-pi-ai-hat-plus.png" alt="Raspberry Pi AI HAT+ 26 TOPS" 
class="component-image">
    <i>Raspberry Pi AI HAT+ 26 TOPS</i>
</div>
mkdocs-only-end -->

Para la instalación, empleamos las dos guías de la documentación oficial de Raspberry Pi, donde se explica cómo instalar el Hailo AI HAT+ [[4](#getting-started-raspberry-pi)] y cómo instalar el software necesario para su funcionamiento [[5](#ai-hat-plus-raspberry-pi)].

1. Verificamos que la Raspberry Pi 5 esté actualizada, sino la actualizamos con el siguiente comando:
    ```bash
    sudo apt update && sudo apt full-upgade
    ```
2. Revisamos la versión actual del firmware instalado en la Raspberry Pi con el siguiente comando:
    ```bash
    sudo rpi-eeprom-update
    ```
	1. Si dicho comando imprime una fecha anterior al 6 de diciembre de 2023, entonces debemos actualizar el firmware de la Raspberry Pi 5. Para ello, ejecutamos el siguiente comando:
	    ```bash
		sudo raspi-config
		```
	2. En el menú de configuración, seleccionamos la opción `Advanced Options` y luego `Bootloader Version`. Elegimos la opción `Latest` y salimos del menú de configuración.
3. Ejecutamos el siguiente comando para actualizar el firmware:
    ```bash
    sudo rpi-eeprom-update -a
    ```
4. Reiniciamos la Raspberry Pi 5 con el siguiente comando:
    ```bash
    sudo reboot
    ```
5. Desconectamos la Raspberry Pi 5 de la corriente y desconectamos todos los dispositivos conectados a ella.
6. Instalamos los espaciadores de la Raspberry Pi 5 utilizando los cuatro tornillos proporcionados. Presionamos firmemente el conector GPIO apilado sobre los pines GPIO de la Raspberry Pi. Desconectamos el cable plano de la AI HAT+ y conectamos el otro extremo al puerto PCIe de la Raspberry Pi. Levantamos el soporte del cable plano desde ambos lados, luego insertamos el cable con los puntos de contacto de cobre hacia adentro, hacia los puertos USB. Con el cable plano completamente insertado en el puerto PCIe, empujamos el soporte del cable hacia abajo desde ambos lados para asegurar el cable plano firmemente en su lugar.
7. Colocamos la AI HAT+ sobre los espaciadores y utilizamos los cuatro tornillos restantes para asegurarla en su lugar.
8. Conectamos el cable plano a la AI HAT+ y lo aseguramos en su lugar. Para ello, levantamos el soporte del cable plano desde ambos lados, luego insertamos el cable con los puntos de contacto de cobre hacia arriba. Con el cable plano completamente insertado en el puerto PCIe, empujamos el soporte del cable hacia abajo desde ambos lados para asegurar el cable plano firmemente en su lugar.
9. Conectamos la Raspberry Pi 5 a la corriente y encendemos el dispositivo.
10. Para habilitar velocidades PCIe Gen 3.0 [[6](#computers-raspberry-pi)], ejecutamos el siguiente comando:
    ```bash
    sudo raspi-config
    ```
	1. En el menú de configuración, seleccionamos la opción
	   `Advanced Options` y luego `PCIe Speed`. Elegimos la opción
	   `Yes` para habilitar el modo PCIe Gen 3.0.
	2. Reiniciamos la Raspberry Pi 5.
11. Instalamos las dependencias requeridas para usar el NPU. Ejecutamos el siguiente comando desde una ventana de terminal:
    ```bash
    sudo apt install hailo-all
    ```
    Cabe destacar que, debido a que la última actualización (4.21.0) es muy reciente, recomendamos instalar la versión anterior que es con la que hemos podido trabajar y comprobar su correcto funcionamiento, para lo cual, en vez del anterior comando, sería:
    ```bash
    sudo apt install hailo-all=4.20.0
    ```
    Esto instalará las siguientes dependencias:
	- Controlador de dispositivo del kernel Hailo y firmware
	- Software de middleware HailoRT
	- Bibliotecas de postprocesamiento central Tappas de Hailo
	- Etapas de software de demostración de postprocesamiento rpicam-apps Hailo
12. Finalmente, reiniciamos la Raspberry Pi de nuevo para que estos ajustes tengan efecto.
13. Para verificar que el NPU está correctamente instalado y funcionando, ejecutamos el siguiente comando:
    ```bash
    hailortcli fw-control identify
    ```
    Si el NPU está correctamente instalado, deberíamos ver un mensaje similar al siguiente:
    ```bash
    Executing on device: 0001:01:00.0
    Identifying board
    Control Protocol Version: 2
    Firmware Version: 4.20.0 (release,app,extended context switch buffer)
    Logger Version: 0
    Board Name: Hailo-8
    Device Architecture: HAILO8
    Serial Number: <N/A>
    Part Number: <N/A>
    Product Name: <N/A>
    ```

## Configuración de la Raspberry Pi

<!-- github-only-start -->
<p align="center">
	Raspberry Pi 5
	<br>
	<i>Raspberry Pi 5</i>
</p>
<!-- github-only-end -->

<!-- mkdocs-only-start
<div class="hcenter">
    <img src="/assets/images/components/raspberry-pi-5.png" alt="Raspberry Pi 5" 
class="component-image">
    <i>Raspberry Pi 5</i>
</div>
mkdocs-only-end -->

Para configurar la Raspberry Pi, primero conectamos la Raspberry Pi a un monitor, teclado y ratón.

Luego, encendemos la Raspberry Pi y esperar a que se inicie el sistema operativo.

Después, abrimos una terminal y ejecutar el siguiente comando para actualizar el sistema operativo:

```bash
sudo apt update && sudo apt upgrade -y
```

Clonamos el repositorio en el caso de que no se haya realizado aún. Puedes ver las distintas formas de clonar el repositorio en la sección referente al [GitHub](../../github.es.md#repositorio).

Navegamos al directorio del repositorio clonado, en el caso de haberlo clonado en la carpeta de Documentos, el comando sería:

```bash
cd ~/Documents/klevor
```

Cambiamos el directorio actual a `devices/raspberry_pi_5` para acceder al código específico de la Raspberry Pi 5:

```bash
cd devices/raspberry_pi_5
```

Configuramos el entorno virtual de Python. Para ello, ejecuta el siguiente comando:

- Si el sistema operativo es Windows:
    ```cmd
    python -m venv .venv
    .\.venv\Scripts\activate
    ```
- Si el sistema operativo es Linux o macOS:
    ```bash
    python3 -m venv .venv
    source .venv/bin/activate
    ```

Instalamos las dependencias necesarias para el proyecto ejecutando el siguiente comando:

```bash
pip install -r requirements.txt
```

En el caso de no tener configurado la Raspberry Pi Pico 2 W, se recomienda seguir su respectiva [guía de configuración](raspberry-pi-pico-2w.es.md#configuración) para poder utilizarla como controlador del robot. Al igual que, en el caso de no haber generado el modelo para la detección de obstáculos, se recomienda seguir la [guía de configuración del modelo](object-detection.es.md) para poder utilizarlo con la Raspberry Pi 5.

### Configurar el Startup Service

Para que el robot se inicie automáticamente al encender la Raspberry Pi, es necesario configurar un servicio de inicio.

Para ello, nos aseguramos primero de que el script de Shell `run.sh` sea ejecutable, para lo cual ejecutamos el siguiente comando:

```bash
chmod +x run.sh
```

> [!NOTE]
> Necesitamos estar en el directorio `devices/raspberry_pi_5` para que el comando anterior funcione correctamente.

Posteriormente, creamos un archivo de servicio en el directorio `/etc/systemd/system/` con el nombre `klevor.service` con el siguiente comando:

```bash
sudo nano /etc/systemd/system/klevor.service
```

En el editor de texto, pegamos el siguiente contenido:

```ini
[Unit]
Description=Klevor Startup Service
After=multi-user.target

[Service]
User=pi
ExecStart=/home/pi/Documents/klevor/devices/raspberry_pi_5/run.sh
WorkingDirectory=/home/pi/Documents/klevor/devices/raspberry_pi_5
StandardOutput=inherit
StandardError=inherit
Restart=on-failure

[Install]
WantedBy=multi-user.target
```

> [!NOTE]
> Reemplazamos `user` por el nombre de usuario de la Raspberry Pi, que por defecto es `pi`. Así mismo, reemplazamos `/home/pi/Documents/klevor/devices/raspberry_pi_5/run.sh` con la ruta completa al script `run.sh` que se encuentra en el directorio del repositorio clonado. De igual forma, ajustamos la ruta del `WorkingDirectory` al directorio donde se encuentra el script `run.sh`.

Guardamos los cambios y salimos del editor de texto (en nano, presionamos `Ctrl + X`, luego `Y` para confirmar los cambios y finalmente `Enter`).

Luego, recargamos los servicios del sistema con el siguiente comando:

```bash
sudo systemctl daemon-reload
```

Finalmente, habilitamos el servicio para que se inicie automáticamente al arrancar la Raspberry Pi con el siguiente comando:

```bash
sudo systemctl enable klevor.service
```

> [!NOTE]
> Si en algún momento necesitas detener el servicio, puedes hacerlo con el siguiente comando:	
> ```bash
> sudo systemctl stop klevor.service	
> ```

Reiniciamos la Raspberry Pi para que los cambios surtan efecto. A partir de ahora, el robot se iniciará automáticamente al encender la Raspberry Pi.

> [!IMPORTANT]
> Por la lógica del código, el robot no se moverá hasta que sea pulsado el botón o switch de encendido, como se indica en el diagrama de conexiones del robot. Esto es para evitar que el robot se mueva accidentalmente al encender la Raspberry Pi. Puedes ver el diagrama de conexiones en la sección de [Electrónica](../../electronic/diagrams/wiring.es.md).

> [!IMPORTANT]
> En el caso de que creas que el robot no se haya iniciado correctamente, puedes revisar el estado del servicio con el siguiente comando:
> ```bash
> sudo systemctl status klevor.service
> ```
> Así mismo, puedes ejecutar el código directamente sin necesidad de configurar el servicio de inicio, para lo cual, simplemente ejecuta el siguiente comando:
> ```bash
> run.sh
> ```
> Esto iniciará el robot y podrás ver los mensajes de depuración en la terminal. Si todo funciona correctamente, deberías ver mensajes indicando que el robot está listo para recibir comandos.
> Si deseas detener el robot, puedes presionar `Ctrl + C` en la terminal donde se está ejecutando el script `run.sh`.

# Referencias

1. *Raspberry Pi OS*. (2025). Raspberry Pi. <a id="raspberry-pi-os" href="https://www.raspberrypi.com/software/">https://www.raspberrypi.com/software/</a>

2. *Raspberry Pi Connect*. (2025). Raspberry Pi. <a id="raspberry-pi-connect" href="https://www.raspberrypi.com/documentation/remote-access/raspberry-pi-connect.html">https://www.raspberrypi.com/documentation/remote-access/raspberry-pi-connect.html</a>

3. *Camera*. (2025). Raspberry Pi. <a id="camera-docs" href="https://www.raspberrypi.com/documentation/computers/camera.html">https://www.raspberrypi.com/documentation/computers/camera.html</a>

4. *AI Kit and AI HAT+ software*. (2025). Raspberry Pi. <a id="getting-started-raspberry-pi" href="https://www.raspberrypi.com/documentation/computers/ai.html#getting-started">https://www.raspberrypi.com/documentation/computers/ai.html#getting-started</a>

5. *AI Hat+*. (2025). Raspberry Pi. <a id="ai-hat-plus-raspberry-pi" href="https://www.raspberrypi.com/documentation/accessories/ai-hat-plus.html#ai-hat-plus">https://www.raspberrypi.com/documentation/accessories/ai-hat-plus.html#ai-hat-plus</a>

6. *Raspberry Pi*. (2025). Raspberry Pi. <a id="computers-raspberry-pi" href="https://www.raspberrypi.com/documentation/computers/raspberry-pi.html">https://www.raspberrypi.com/documentation/computers/raspberry-pi.html</a>

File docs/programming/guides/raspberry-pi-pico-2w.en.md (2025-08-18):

# Raspberry Pi Pico 2 W Guide

*In Development*

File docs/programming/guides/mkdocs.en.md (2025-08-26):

# MkDocs Guide

<!-- github-only-start -->
<p align="center">
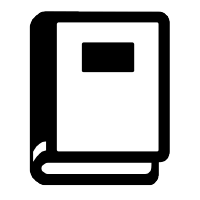
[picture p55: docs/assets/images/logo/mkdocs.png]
MkDocs' Logo
	
	<br>
	<i>MkDocs' Logo</i>
</p>
<!-- github-only-end -->

<!-- mkdocs-only-start
<div class="hcenter">
    <img src="/assets/images/logo/mkdocs.png" alt="MkDocs' Logo" 
class="logo--3rd-party">
    <i>MkDocs' Logo</i>
</div>
mkdocs-only-end -->

In this section we present a guide to install Mkdocs and serving documentation made with the library, a static documentation tool that allows to generate websites from Markdown files.

## Installation

To install MkDocs, you need to have `Python` and `pip` installed in your system. Also, it is needed to install all of the libraries' dependencies. To simplify the installation process, we created a `requirements.txt` which contains all of the project's dependencies

You can create a Python virtual environment, install MkDocs and the project's dependencies by executing this command in the terminal:

- If the operating system is Windows:

```cmd
python -m venv .venv
./.venv/Scripts/activate
pip install -r requirements.txt
```
- If the operating system is Linux or macOS:

```bash
python3 -m venv .venv
source .venv/bin/activate
pip install -r requirements.txt
```

## Serve Documentation

Once you have installed MkDocs and the project's dependencies, you can serve the documentation locally by executing the following command in the terminal:

```bash
mkdocs serve
```

> [!IMPORTANT]
> If you want to serve the documentation from another terminal, it's necessary to activate Python's virtual environment again, because MkDocs depends on the dependencies installed on the virtual environment. You can do this with this command:
> - If the operating system is Windows:
> ```cmd
> .env\Scripts\activate
> ```
> 
> - If the operating system is Linux or macOS:
> ```bash
> source .venv/bin/activate
> ```

However, if you want to simplify the process, simply execute the `serve.bat` file in Windows or `serve.sh` in Linux or macOS, which will activate the virtual environment and serve the documentation automatically.

## Deployment

To deploy the documentation in GitHub Pages, use the following command:

```bash
mkdocs gh-deploy
```

> [!NOTE]
> This command will create a branch named `gh-pages` in your GitHub repository and will deploy the documentation on that branch. Make sure your repository is configured to use GitHub Pages from the `gh-pages` branch.

> [!IMPORTANT]
> This command will only work if the repository you want to create the branch on, is **not** Team Steel Bot's official repository, basically, it must be a fork of this repository to be able to deploy GitHub Pages, this is because, users external to the project don't have the permissions necessary to do any kind of modification to the aforementioned repository.

However, to simplify the deployment process, you can execute the `deploy.bat` file in Windows or `deploy.sh` in Linux or macOS, which will deploy the documentation automatically. In this project, this `.bat`or `.sh` will deploy the documentation to said branch both to the official public remote repository and also our internal developping repository.

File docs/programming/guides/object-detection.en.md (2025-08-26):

# Object Detection Guide

## Model Creation

<!-- github-only-start -->
<p align="center">
    GitHub's Logo
    <br>
    <i>GitHub's Logo</i>
</p>
<!-- github-only-end -->

<!-- mkdocs-only-start
<div class="hcenter">
    <img src="/assets/images/logo/github.png" alt="GitHub's Logo" 
class="logo--3rd-party">
    <i>GitHub's Logo</i>
</div>
mkdocs-only-end -->

To start, download our GitHub repository, where you can find the object detection model's code, as well as their scripts necessary for its training and converstion to a compatible format with the Hailo 8. To do so, we recommend to head to the documentation's next section [```GitHub```](../../github.en.md#repository), where we explain all of the different ways you can download the repository, like downloading the `.zip` folder or by just cloning the repository with Git.

After downloading the repository, head to the folder `devices/raspberry-pi-5/src`, where you can find all of the code used by the Raspberry Pi 5, which can be done with the following command:

```bash
cd devices/raspberry-pi-5/src
```

> [!WARNING]
> To make sure said command works properly, the route must be relative to the folder where the cloned repository is. In the case it's not in the repository's root folder, the route must be modified accordingly.

Afterwards, move to the `yolo/scripts` folder:

```bash
cd yolo/scripts
```

Create a Python virtual environment with the following commands:

- If the operating system is Windows:
    ```cmd
    python -m venv .venv
    ./.venv/Scripts/activate
    pip install -r requirements.txt
    ```
- If the operating system is Linux:
    ```bash
    python -m venv .venv
    source .venv/bin/activate
    pip install -r requirements.txt
    ```

To create the dataset, we took images of the prisms that will be used in the competition. These images were taken from multiple devices, in different light conditions and angles, these images are saved in the folder `yolo/dataset/general/original/to_process`.

Then we run the script `yolo/scripts/resize.py` to resize all of the images to 640 x 640 pixels, which is the input size for the YOLOv11 model. This script uses the OpenCV library to resize the images and save them in the `yolo/dataset/general/resized/to_process`.

<!-- github-only-start -->
<div>
    <p align="center">
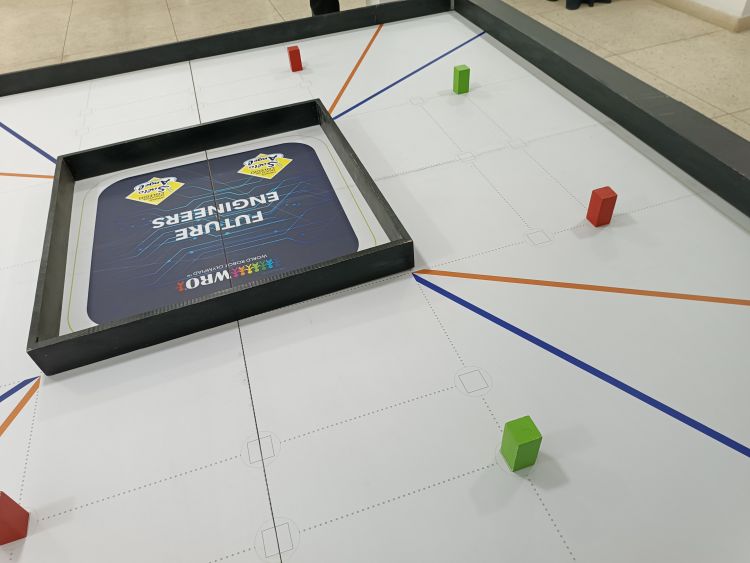
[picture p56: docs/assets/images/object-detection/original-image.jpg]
Non-resized image from dataset
        
        <br>
        <i>Non-resized image from dataset</i>
    </p>
    <br>
    <p align="center">
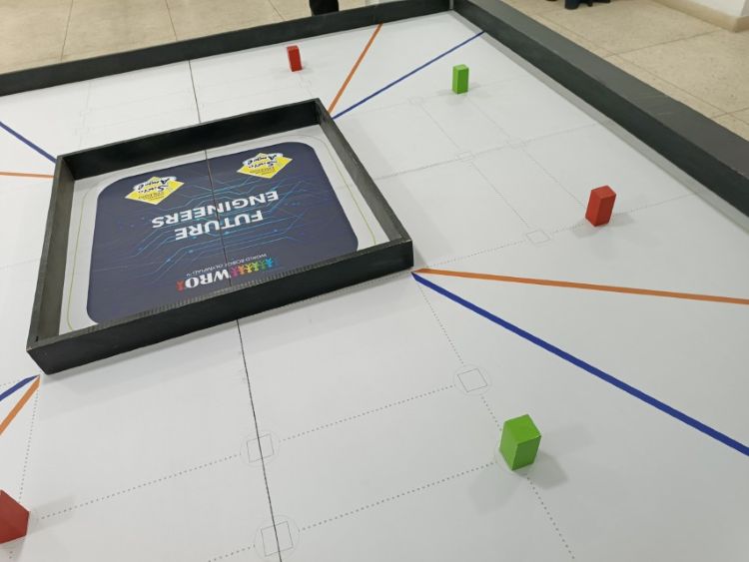
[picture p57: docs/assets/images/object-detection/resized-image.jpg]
Resized image from dataset
        
        <br>
        <i>Resized image from dataset</i>
    </p>
</div>
<!-- github-only-end -->

<!-- mkdocs-only-start
<div class="center image-comparison-container">
    <div class="hcenter">
       <img src="/assets/images/object-detection/original-image.jpg" alt="Non-resized image from dataset" class="object-detection-image">
       <i>Non-resized image from dataset</i>
    </div>
    <div class="hcenter">
       <img src="/assets/images/object-detection/resized-image.jpg" alt="Resized image from dataset" class="object-detection-image">
       <i>Resized image from dataset</i>
    </div>
</div>
mkdocs-only-end -->

Afterwards, the images were annotated, where the prisms were labeled with their respective colors. To do so, we used [Label Studio](https://labelstud.io/), a data labelling open-source tool that allows to create custom datasets to train Deep Learning models automatically.

> [!WARNING]
> If the number of images to label is big enough, Label Studio will return an error `The number of files exceeded settings.DATA_UPLOAD_MAX_NUMBER_FILES`. To fix this, if Label Studio is installed as a Python package, you can modify the file `settings.py` which is located in the folder `label_studio/core/settings.py`, change the value of `DATA_UPLOAD_MAX_NUMBER_FILES` to a number bigger than the number of images to label or `None` if you wish for an unlimited option. In case you can't find this file, search in the folder `site-packages/label_studio/core/settings.py` inside of Python's virtual environment where Label Studio was installed.

<!-- github-only-start -->
<p align="center">
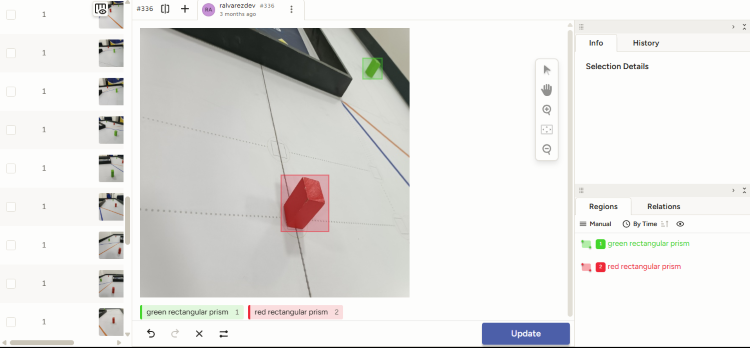
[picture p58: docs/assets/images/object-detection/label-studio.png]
Labelling images with Label Studio
   
   <br>
   <i>Labelling images with Label Studio</i>
</p>
<!-- github-only-end -->

<!-- mkdocs-only-start
<div class="hcenter">
   <img src="/assets/images/object-detection/label-studio.png" alt="Labelling images with Label Studio" class="object-detection-image">
   <i>Labelling images with Label Studio</i>
</div>
mkdocs-only-end -->

During this process, we handle data sets for 1 (**G**, **M**, **R**), 2 (**GR**), 3 (**GMR**), 4 (**BGOR**) classes, which we switched during the project's development, **M** comes from `magenta rectangular prism`, **G** comes from `green rectangular prism`, **R** comes from `red rectangular prism`, **B** comes from `blue line` and **O** comes from `orange line`. Initially, we tried to build a 4-class model, however, it didn't meet our performance standards, aside from
including the green and red prism, it also included the blue and orange line, however, since we knew which way to turn thanks to the RPLiDAR C1's measurements, we decided to omit the classes for the blue and orange lines, since they weren't really needed. Afterwards, we built a 2-class model, which was capable of detecting the red and green prisms. Right after, we built a 3-class model, this extra class is to detect the magenta prism, to properly detect the parking spot. Then, we opted to use 2 models, one with two classes (**GR**), to detect the game field obstacles, and a 1-class model (**M**) to detect the parking spot after completing all of the tasks. Finally, due to certain optimization issues with the Hailo 8, we just used 3 models with just 1 class each (**G**, **M**, **R**), with this, each model was capable of detecting their respective prism, we simply used one model or the other according to what is required in the challenge.

Now, we will explain the steps necessary to assemble the object detection models, we will use the 1-class model (**G**) as an example, however, the steps are essentially the same for the other models, just change the image's route and the class number.

It's worth mentioning that, just as we vary the classes number, we also vary the amount of number of images per class, from a dataset with around 350 images before doing the *data augmentation*, to a dataset with about 1300 images before doing the *data augmentation*, where each image was labeled manually by a team's member to train the model accurately.

After labelling the images with Label Studio, the labels were exported in the YOLO format and were saved in the `yolo/dataset/g/labeled/to_process` folder. Right after, the `yolo/scripts/augment.py` script was run to generate roughly 10 augmented images per unaugmented image, using the library OpenCV. This script applies differet changes to the images, such as rotation, scaling, translation, brightness and contrast, to increase the variety of the data set and increase the model's performance. Finally, run the script `yolo/scripts/after_labeling.py` to move the images from the `yolo/dataset/g/augmented` folder to the `yolo/dataset/g/labeled/processed` folder.

Afterwards, run the script `yolo/scripts/split.py` to separate the data set into a training set `yolo/dataset/g/organized/train`, a validation set `yolo/dataset/g/organized/val` and a test set `yolo/dataset/g/organized/test` with a distribution around 70%, 20% and 10%, respectively. This script uses the library `os` to create the necessary folders and move the images to the corresponding folders, however it will not modify or delete the folders `yolo/dataset/g/labeled/to_process` and `yolo/dataset/g/labeled/processed`.

> [!NOTE]
> You can observe, that, inside each of the routes, you can find the `to_process` folder, this is just a temporary folder that is used to save the images that are being processed. Once the images are processed, the files inside of them are moved to their corresponding `processed` folder, which is located in the same route. This way, we avoid that the processed images get mixed up with the unprocessed image, while keeping the door open to train the same model, without needing to process the same images. Also, you can observe that both for `augmented` and `organized`, the `to_process` folder doesn't exist, because, after these images are processed, they are deleted because of the large number of them at the moment of doing the `data_augmentation`.

## Model Training

<!-- github-only-start -->
<p align="center">
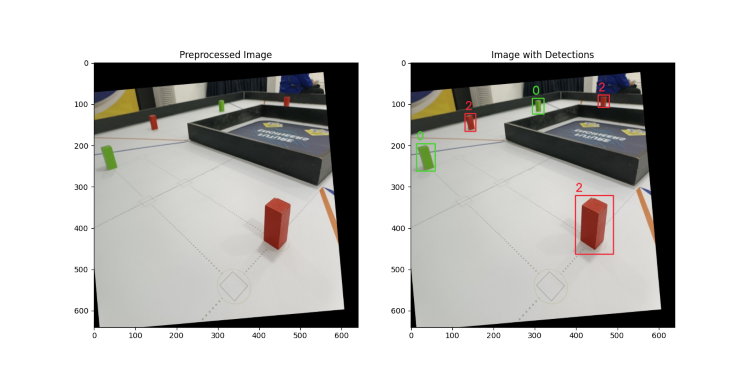
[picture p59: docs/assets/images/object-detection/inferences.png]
Image with different infrerences made (GMR model)
   
   <br>
   <i>Image with different infrerences made (GMR model)</i>
</p>
<!-- github-only-end -->

<!-- mkdocs-only-start
<div class="hcenter">
   <img src="/assets/images/object-detection/inferences.png" alt="Image with different infrerences made (GMR model)" class="object-detection-image">
   <i>Image with different infrerences made (GMR model)</i>
</div>
mkdocs-only-end -->

First, depending on the model and the way it's gonna be trained, a `.yaml` file has to be modified, which are located inside of the folder `yolo/data`. Modify the image's route and the labels to the corresponding routes. In this case. we have to modify the `g.yaml` file for the 1-class model, whose parent folder will vary between `colab` and `local` depending on the environment.

> [!NOTE]
> At the moment of cloning this repository, we provide template files for the `.yaml`, these end in `yaml.example`. After you modify them, their extension has to be reverted back to a `.yaml` file.

There are two ways of training a model depending on the resources available in the moment:

1. **Local Training**: To do this, you need to have a GPU dedicated exclusively to training the model.
    1. In this case, run the script `yolo/scripts.train.py` to train the YOLOv11 model. This script uses the library [Ultralytics](../libraries/python.en.md#ultralytics-yolo) to train the model and save the weights in the folder `yolo/v11/runs/g`.
2. **Remote Training**: To do this, you can use [Google Colab](https://colab.research.google.com/), where you can use a GPU for free or for a fee, depending on the time required for training and how fast you want the training to be done in.
    1. In this case, run the script `yolo/scripts/zip_to_train.py`, which will create a compressed file with the data set, which will be moved to the folder `yolo/v11/zip`.
    2. Later, we upload the file to Google Drive, change the visibility to `Anyone with the link can view` and copy the ID of the compressed file, which is found in its URL. We paste this link in the corresponding section of Jupyter Notebook `yolo/v11/notebooks/colab/g_train.ipynb` to be able to download the compressed file in Google Colab.
    3. Select the runtime environment according to the availability. You can use a NVIDIA Tesla T4 GPU for free for roughly 5 h daily, or buying 100 credits (which cost around $10 at the time of writing this guide) from this platform to use it for longer and/or using better GPUs. In our case, we used a NVIDIA Tesla L4, which consumed 6 credits to train a complete model.
    4. Run the Jupyter Notebook sections `yolo/v11/notebooks/colab/g_train.ipynb`, omitting the aforementioned section related to the decompression of the compressed file. This Jupyter Notebook uses the library [Ultralytics](../libraries/python.en.md#ultralytics-yolo) to do the model's training and save the weights in the folder `yolo/v11/runs/g`.
    5. Once the training is done, you can download the compressed file with the weights of the model from Google Drive and decompress it in the folder `yolo/v11/runs/g` locally.
3. **Inference**: Run the script `yolo/scripts/test.py` to do the trained model's inference and evaluate the model's performance with images it hasn't seen. This script generates images with the inferences made by the model, where the bounding boxes and labels are shown for each detected object.
4. **ONNX**: Run the script `yolo/scripts/export.py`, and change the model's format to `onnx`, which is an open format used to represent Machine Learning models in an interoperable way between different frameworks, tools, among others [[2](#onnx)].
5. **Clean-up**: Finally, run the script `yolo/scripts/after_training.py` to delete the folder `yolo/dataset/g/organized/val`, because these will not be needed for further steps. Also, it will move the content from the folder `yolo/dataset/g/organized/train/images` to the subdirectory in `hailo/suite/train`, to delete the first one. Also, so that the model can be converted to a format compatible with Hailo 8, it will move the best-performing `ONNX` format weights corresponding to the model.

> [!TIP]
> In the ocurrence that you are using Google Colab and the session disconnects in the runtime environment during the model's training, you can resume the training by modifying the model route or the name of the model to use in the Notebook's function `train_model` by the route where the best training weights were saved, in our case: `g_to_train/yolo/v11/runs/m/weights/best.pt`.

<!-- github-only-start -->
<p align="center">
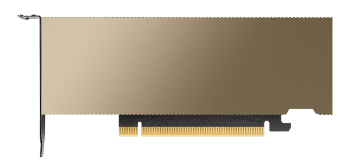
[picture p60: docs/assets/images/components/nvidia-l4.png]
NVIDIA Tesla L4 GPU Front View
   
   <br>
   <i>NVIDIA Tesla L4 GPU Front View</i>
</p>
<!-- github-only-end -->

<!-- mkdocs-only-start
<div class="hcenter">
   <img src="/assets/images/components/nvidia-l4.png" 
alt="NVIDIA Tesla L4 GPU Front View" class="component-image">
    <i>NVIDIA Tesla L4 GPU Front View</i>
</div>
mkdocs-only-end -->

> [!IMPORTANT]
> During this section, YOLO's version 11 is mentioned, since we used this version, but, in the same way as we mentioned the data set **G** for didactic purposes, you can use any YOLO version, and any dataset, since the process is essentially the same. However, it is recommended to use YOLOv11, because it's the most recent version (at the time of writing) and has significant upgrades compared with previous versions.

## Model Conversion

To convert the model to a compatible format with the Hailo 8, we require using Docker (but it is not essential), to create a container with all the necessary packages for its proper functioning.

<!-- github-only-start -->
<p align="center">
    Docker's Logo
    <br>
    <i>Docker's Logo</i>
</p>
<!-- github-only-end -->

<!-- mkdocs-only-start
<div class="hcenter">
    <img src="/assets/images/logo/docker.png" alt="Docker's Logo" 
class="logo--3rd-party">
    <i>Docker's Logo</i>
</div>
mkdocs-only-end -->

When installing the AI HAT+, run the command `hailortcli fw-control identify`, where you noticed the following line:

```
Firmware Version: 4.20.0 (release,app,extended context switch buffer)
```

As you can observe, in our case, our firmware version is 4.20.0, which is why we have to make sure that the Dataflow Compiler, is compatible with this version. For example, due to a certain change in the Dataflow Compiler for the 3.31.0 version, where different mechanisms for the error detection are different, the HailoRT's older versions (before 4.21.0) will not be capable of executing compiled HEF files due to DataFlow Compiler's new version [[3](#2025-04-hailo)]. We recommend checking out the [Compatibility Table](https://hailo.ai/developer-zone/documentation/hailo-sw-suite-2025-04/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), to know which packages' versions to install to avoid compatibility issues.

First, visit Hailo's official page, where you have to create an account, log in, and head on the developer zone. Here, select the software download section, and download the necessary packages [[1](#custom-dataset-medium)]

- HailoRT, for the architecture where Docker is being run on (in our case, `amd64`). Recommended version: 4.20.0.
- HailoRT Python package (whl), for the architecture where Docker is being run on (in our case, x86_64), and the Python container version (if its not being modified, it has to be the version 3.10). Recommended version: 4.20.0.
- Hailo Dataflow Compiler, for the architecture Docker is being run on (in our case, `x86_64`). Recommended version: 3.30.0.

> [!IMPORTANT]
> If you are using a NVIDIA GPU to optimize the `.har` format, you also have to install the [NVIDIA Container Toolkit](https://docs.nvidia.com/datacenter/cloud-native/container-toolkit/install-guide.html)

> [!IMPORTANT]
> If you can't find any of the packages, inside the section to download Hailo software, there are two ways to search the packages: `Latest releases` and `Archive`; the first one is the predetermined. If you can't find the respective package in `Latest releases`, it probably is in `Archive`.

Then, we switch directories:

- If you have a GPU, go to the directory `hailo/suite/dockerfiles/gpu`, with the command:
    ```bash
    cd hailo/suite/dockerfiles/gpu
    ```
- If you don't have a GPU, go to this directory instead: `hailo/suite/dockerfiles/no-gpu`.
    ```bash
    cd hailo/suite/dockerfiles/no-gpu
    ```

Either way, there should be a file named `Dockerfile`, indifferent from which folder are we in.

To create the Docker image, run the following command:

```bash
docker build -t hailo_compiler:v0 .
```

Wait until all dependencies are installed and the container's Docker image is ready.

Afterwards, initialize the Docker container:

- In case you have a GPU:
    ```bash
    docker run -it --name compile_onnx_file --gpus all --ipc=host -v {path}:/home/hailo/shared hailo_compiler:v0
    ```

- In case you don't have a GPU:
    ```bash
    docker run -it --name compile_onnx_file --ipc=host -v {path}:/home/hailo/shared hailo_compiler:v0
    ```

> [!NOTE]
> Replace `path` with the absolute route for `hailo/suite`.

Inside of the container, move to the directory `/home/hailo/shared/libs`:

```bash
cd /home/hailo/shared/libs
```

In the same terminal, create a Python Virtual Environment:

```bash
python -m venv .venv
source .venv/bin/activate
```

Now install the pacakges previously downloaded, which are found inside the folder `hailo/suite/libs`. For the versions downloaded, run the following command:

```bash
dpkg -i hailort_4.20.0_amd64.deb
pip install  hailort-4.20.0-cp310-cp310-linux_x86_64.whl
pip install hailo_dataflow_compiler-3.30.0-py3-none-linux_x86_64.whl
```

Clone this GitHub repository, it all the necessary files to convert the model from `ONNX` format to `HEF`:

```bash
git clone https://github.com/hailo-ai/hailo_model_zoo.git
```

However, since we need the 2.14 version, the command would be the following:

```bash
git clone -b v2.14 https://github.com/hailo-ai/hailo_model_zoo.git
```

Move from the current directory to the `hailo-model-zoo` corresponding:

```bash
cd hailo_model_zoo
```

Install all the required dependencies:

```bash
pip install -e .
```

> [!WARNING]
> If you get an error like:
> ```bash
> ERROR: pip's dependency resolver does not currently take into account all the packages that are installed. This behaviour is the source of the following dependency conflicts. 
> tensorflow 2.12.0 requires numpy<1.24,>=1.22, but you have numpy 2.2.6 which is incompatible. 
> hailo-dataflow-compiler 3.30.0 requires numpy==1.23.3, but you have numpy 2.2.6 which is incompatible.
> ```
> Modify the file `setup.py` which is found inside of the repository, and, in the line 44, inside of the `main` function, substitute `"numpy"` with `"numpy==1.23.3"`, and in the line 46, substitute `"scipy"` with `"scipy==1.9.3"`. Retry the command:
> ```bash
> pip install -e .
> ```

Check if the packages were installed correctly with the following command:

```bash
hailomz --version
```

Modify the model configuration file, in the field `classes`, establishing the number of classes that were trained with the model in questionj (for example, for the model **G** it would be 1):

```bash
sudo nano hailo_model_zoo/cfg/postprocess_config/yolov11n_nms_config.json
```

Establish the variable of the environment `USER` as Hailo:

```bash
export USER=hailo
```

Now, to convert the model to a compatible format with the Hailo 8, run the following commands:

- First, parse the model:
    ```bash
    hailomz parse --ckpt ~hailo/shared/v11/g/best.onnx --hw-arch hailo8 yolov11n
    mv yolov11n.har g_parsed.har
    ```

- Second, optimize the model:
    ```bash
    hailomz optimize --har g_parsed.har --classes 2 --calib-path ~hailo/shared/train --hw-arch hailo8 yolov11n
    mv yolov11n.har g_optimized.har
    ```

- Finally, compile the model:
    ```bash
    hailomz compile --har g_optimized.har --hw-arch hailo8 yolov11n
    mv yolov11n.hef g_compiled.hef
    ```

wait until the previous step is completed, and we can have our custom and Hailo 8 compatible model ready.

To move all of the files generated in the directory `hailo/suite/libs/hailo_model_zoo` to the folder with the corresponding model's weights, run the script `yolo/scripts/after_hailo_compilation.py`.

Finally, to exit the Docker container, run the following command:

```bash
exit
```

## Model Test

After completing all of the previous steps, move to the folder `hailo/suite/libs`, and clone the following repository:

```bash
git clone https://github.com/hailo-ai/hailo-rpi5-examples.git
```

Change the directory again, move to `hailo-rpi5-examples`, with the following command:

```bash
cd hailo-rpi5-examples
```
Run the following command to install all of the necessary dependencies:

```bash
./install.sh
```

Now, every time you open a new terminal, run the following command:

```bash
source setup_env.sh
```

In this moment, we can test that everything is working correctly, like the model's precision:

- If you have a camera with a CSI port compatible with the Raspberry Pi, after connecting it, run the following command:
    ```bash
    python basic_pipelines/detection.py --input rpi --labels-json ../labels/g.json --hef-path ../../v11/runs/g/weights/compiled.hef
    ```

- If you don't have a camera hwoever, you can use the following command to test the model with a test image:
    ```bash
    python basic_pipelines/detection.py --input {image} --labels-json ../labels/g.json --hef-path ../../v11/runs/g/weights/compiled.hef
    ```

> [!NOTE]
> Substitute `image` with the test image's route.

This will open a window with the camera, where it will show the bounding boxes and the labels of the detected objects. If everything is working correctly, we should see the objects being detected in real time.

# References

1. d'Oleron, L. (April 23rd, 2025). *Custom dataset with Hailo AI Hat, Yolo, Raspberry PI 5, and Docker*. Medium. <a id="custom-dataset-medium" href="https://pub.towardsai.net/custom-dataset-with-hailo-ai-hat-yolo-raspberry-pi-5-and-docker-0d88ef5eb70f">https://pub.towardsai.net/custom-dataset-with-hailo-ai-hat-yolo-raspberry-pi-5-and-docker-0d88ef5eb70f</a>

2. *ONNX*. (2025). ONNX. <a id="onnx" href="https://onnx.ai/">https://onnx.ai/</a>

3. *2025-04 | Hailo*. (2025). Hailo. <a id="2025-04-hailo" href="https://hailo.ai/developer-zone/documentation/hailo-sw-suite-2025-04/?sp_referrer=suite/suite_changelog.html">https://hailo.ai/developer-zone/documentation/hailo-sw-suite-2025-04/?sp_referrer=suite/suite_changelog.html</a>

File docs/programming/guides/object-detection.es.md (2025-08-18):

# Guía de Detección de Objetos

## Creación del Modelo

<!-- github-only-start -->
<p align="center">
	Logo de GitHub
	<br>
	<i>Logo de GitHub</i>
</p>
<!-- github-only-end -->

<!-- mkdocs-only-start
<div class="hcenter">
    <img src="/assets/images/logo/github.png" alt="Logo de GitHub" 
class="logo--3rd-party">
    <i>Logo de GitHub</i>
</div>
mkdocs-only-end -->

Para empezar, debemos descargamos nuestro repositorio de GitHub, donde se encuentra el código del modelo de detección de objetos, así como los scripts necesarios para su entrenamiento y conversión a un formato compatible con el Hailo 8. Para ello, recomendamos dirigirse a la siguiente sección de la documentación [```GitHub```](../../github.es.md#repositorio), donde se explican las distintas formas de descargar el repositorio, ya sea mediante la descarga del archivo comprimido o mediante la clonación del repositorio con Git.

Después de haber descargado el repositorio, debemos dirigirnos a la carpeta `devices/raspberry-pi-5/src`, donde se encuentra todo el código empleado por la Raspberry Pi 5, puede realizarse con el siguiente comando:

```bash
cd devices/raspberry-pi-5/src
```

> [!WARNING]
> Para que dicho comando funcione correctamente, la ruta debe ser relativa a la carpeta donde se encuentra el repositorio clonado. En caso de no estar en la carpeta raíz del repositorio, se debe modificar la ruta acorde a la ubicación del mismo.

Posteriormente, nos movemos a la carpeta `yolo/scripts`:

```bash
cd yolo/scripts
```

Creamos un entorno virtual de Python con los siguientes comandos:

- Si el sistema operativo es Windows:
    ```cmd
    python -m venv .venv
    ./.venv/Scripts/activate
    pip install -r requirements.txt
    ```
- Si el sistema operativo es Linux:
    ```bash
    python -m venv .venv
    source .venv/bin/activate
    pip install -r requirements.txt
    ```

Para la creación del conjunto de datos, tomamos imágenes de los prismas que se utilizarán en la competencia. Estas imágenes fueron tomadas con los distintos dispositivos de nuestro equipo, en distintas condiciones de luz y ángulos, y las cuales guardamos en la carpeta `yolo/dataset/general/original/to_process`.

Luego, ejecutamos el script `yolo/scripts/resize.py` para redimensionar las imágenes a un tamaño de 640 × 640 píxeles, que es el tamaño de entrada del modelo YOLOv11. Este script utiliza la biblioteca OpenCV para redimensionar las imágenes y guardarlas en la carpeta `yolo/dataset/general/resized/to_process`.

<!-- github-only-start -->
<div>
	<p align="center">
		Imagen sin redimensionar del conjunto de datos
		<br>
		<i>Imagen sin redimensionar del conjunto de datos</i>
	</p>
	<br>
	<p align="center">
		Imagen redimensionada del conjunto de datos
		<br>
		<i>Imagen redimensionada del conjunto de datos</i>
	</p>
</div>
<!-- github-only-end -->

<!-- mkdocs-only-start
<div class="center image-comparison-container">
    <div class="hcenter">
       <img src="/assets/images/object-detection/original-image.jpg" alt="Imagen sin redimensionar del conjunto de datos" class="object-detection-image">
       <i>Imagen sin redimensionar del conjunto de datos</i>
    </div>
    <div class="hcenter">
       <img src="/assets/images/object-detection/resized-image.jpg" alt="Imagen redimensionada del conjunto de datos" class="object-detection-image">
       <i>Imagen redimensionada del conjunto de datos</i>
    </div>
</div>
mkdocs-only-end -->

Posteriormente, se realizó la anotación de las imágenes, donde se etiquetaron los prismas con sus respectivos colores. Para ello, se utilizó la herramienta [Label Studio](https://labelstud.io/), una herramienta de etiquetado de datos de código abierto que permite crear conjuntos de datos personalizados para el entrenamiento de modelos de aprendizaje automático.

> [!WARNING]
> Si el número de imágenes por anotar es muy grande, notaremos que la herramienta Label Studio arrojará un error `The number of files exceeded settings.DATA_UPLOAD_MAX_NUMBER_FILES`. Para solucionarlo, si Label Studio fue instalado como un paquete de Python, se puede modificar el archivo `settings.py` que se encuentra en la carpeta `label_studio/core/settings.py`, donde se debe cambiar el valor de `DATA_UPLOAD_MAX_NUMBER_FILES` a un número mayor al número de imágenes por anotar o `None` si se desea un número ilimitado. En caso de no encontrar este archivo, se puede buscar en la carpeta `site-packages/label_studio/core/settings.py` dentro del entorno virtual de Python donde fue instalado Label Studio.

<!-- github-only-start -->
<p align="center">
   Anotación de imágenes con Label Studio
   <br>
   <i>Anotación de imágenes con Label Studio</i>
</p>
<!-- github-only-end -->

<!-- mkdocs-only-start
<div class="hcenter">
   <img src="/assets/images/object-detection/label-studio.png" alt="Anotación de imágenes con Label Studio" class="object-detection-image">
   <i>Anotación de imágenes con Label Studio</i>
</div>
mkdocs-only-end -->

Durante el proceso, manejamos conjunto de datos de 1 (**G**, **M**, **R**), 2 (**GR**), 3 (**GMR**), 4 (**BGOR**) clases, las cuales fuimos variando a lo largo del desarrollo del proyecto, donde **M** proviene de `magenta rectangular prism`, **G** de `green rectangular prism`, **R** de `red rectangular prism`, **B** de `blue line` y **O** de `orange line`. Primeramente, desarrollamos un modelo de 4 clases, sin embargo, no logró un buen rendimiento para todas las clases, ya que incluía, además del prisma rojo y verde, la línea naranja y la línea azul, que finalmente, debido a nuestros componentes, se podían inferir mediante el RPLIDAR C1. Posteriormente, se decidió omitir las clases relacionadas con las líneas de la pista, las cuales no eran necesarias para la detección de los prismas. Luego, se optó por un modelo de 2 clases, el cual fue capaz de detectar los prismas rojo y verde. Seguidamente, se optó por un conjunto de datos de 3 clases, ya que añadimos una clase adicional, el prisma magenta, para poder realizar la detección del estacionamiento. Después, se optó por dos modelos, uno con dos clases (**GR**), para poder detectar los obstáculos de la pista, y otro de una sola clase (**M**) para la detección del estacionamiento después de haber recorrido toda la pista. Finalmente, debido a ciertas complicaciones por la optimización de los modelos para el NPU Hailo 8, se optó por tres modelos de 1 clase (**G**, **M**, **R**), donde cada uno de estos modelos fue capaz de detectar los prismas de un color específico, acorde a lo requerido en la pista.

Ahora, vamos a explicar los pasos necesarios para continuar con el montaje del modelo de detección de objetos, donde se utilizará como ejemplo el modelo de 1 clase (**G**). Sin embargo, los pasos son los mismos para los demás modelos, donde solo se debe cambiar la ruta de las imágenes y el número de clases.

Cabe destacar que, así como variamos el número de clases, también variamos el número de imágenes por clase, desde un dataset de alrededor de 350 imágenes antes de realizar el *data augmentation*, hasta un dataset de alrededor de 1300 imágenes antes de realizar el *data augmentation*, donde cada una fue anotada por algún integrante del equipo de forma manual para entrenar el modelo de la forma más precisa posible.

Después de haber anotado las imágenes con la plataforma Label Studio, se exportaron las anotaciones en formato YOLO y se guardaron en la carpeta `yolo/dataset/g/labeled/to_process`. Posteriormente, se ejecutó el script `yolo/scripts/augment.py` para generar alrededor de 10 imágenes por cada imagen del conjunto de datos, utilizando la biblioteca OpenCV. Este script aplica distintas transformaciones a las imágenes, como rotación, escalado, traslación y cambio de brillo y contraste, para aumentar la variabilidad del conjunto de datos y mejorar el rendimiento del modelo. Las imágenes generadas se guardaron en la carpeta `yolo/dataset/g/augmented`. Finalmente, ejecutamos el script `yolo/scripts/after_labeling.py` para mover las imágenes de la carpeta `yolo/dataset/g/labeled/to_process` a la carpeta `yolo/dataset/g/labeled/processed`.

Luego, se ejecutó el script `yolo/scripts/split.py` para dividir el conjunto de datos en un conjunto de entrenamiento `yolo/dataset/g/organized/train`, un conjunto de validación `yolo/dataset/g/organized/val` y un conjunto de testing `yolo/dataset/g/organized/test`, con una distribución del 70%, 20% y 10%, respectivamente. Este script utiliza la biblioteca `os` para crear las carpetas necesarias y mover las imágenes a las carpetas correspondientes. Además, este script eliminará las imágenes de la carpeta `yolo/dataset/g/augmented`, mas no modificará o eliminará las carpetas `yolo/dataset/g/labeled/to_process` y `yolo/dataset/g/labeled/processed`.

> [!NOTE]
> Se puede observar, que en cada una de las rutas, se encuentra la carpeta `to_process`, la cual es una carpeta temporal, que se utiliza para guardar las imágenes que se están procesando. Una vez que se han procesado las imágenes, los archivos dentro de las mismas se mueven a una carpeta `processed` correspondiente, la cual se encuentra en la misma ruta. De esta forma, se evita que las imágenes procesadas se mezclen con las imágenes por procesar, así como permite a futuro seguir entrenando el mismo modelo, sin necesidad de volver a procesar las mismas imágenes. Así mismo, se puede observar que tanto para `augmented` y `organized`, no existe la carpeta `to_process`, ya que, después de ser procesadas estas imágenes, son eliminadas debido al gran número de estas al momento de realizar el `data augmentation`.

## Entrenamiento del Modelo

<!-- github-only-start -->
<p align="center">
   Imagen con distintas inferencias realizadas (modelo GMR)
   <br>
   <i>Imagen con distintas inferencias realizadas (modelo GMR)</i>
</p>
<!-- github-only-end -->

<!-- mkdocs-only-start
<div class="hcenter">
   <img src="/assets/images/object-detection/inferences.png" alt="Imagen con distintas inferencias realizadas (modelo GMR)" class="object-detection-image">
   <i>Imagen con distintas inferencias realizadas (modelo GMR)</i>
</div>
mkdocs-only-end -->

Primeramente, dependiendo del modelo y la forma en la que se vaya a entrenar el mismo, se debe modificar un archivo `.yaml`, los cuales se encuentran dentro de la carpeta `yolo/data`, donde se debe modificar la ruta de las imágenes y las etiquetas a las rutas correspondientes. En este caso, se debe modificar el archivo `g.yaml` para el modelo de 1 clase, cuya carpeta padre variará entre `colab` y `local` dependiendo del entorno.

> [!NOTE]
> Al momento de clonar este repositorio, se suministran archivos plantilla para los `.yaml`, los cuales terminan en `.yaml.example`. A los cuales posterior a su modificación, se les debe cambiar la extensión a `.yaml`.

Existen dos maneras de entrenar el modelo dependiendo del equipo disponible en el momento:

1. **Entrenamiento de forma local**: Para ello, se debe contar con una GPU dedicada para el entrenamiento.
	1. En este caso, debemos ejecutar el script `yolo/scripts/train.py` para entrenar el modelo YOLOv11. Este script utiliza la librería [Ultralytics](../libraries/python.es.md#ultralytics-yolo) para realizar el entrenamiento del modelo y guardar los pesos en la carpeta `yolo/v11/runs/g`.
2. **Entrenamiento de forma remota**: Para ello, se puede utilizar [Google Colab](https://colab.research.google.com/), donde se puede utilizar una GPU de forma gratuita o de paga, dependiendo del tiempo requerido para el entrenamiento y la velocidad en la que se quiere completar dicho entrenamiento.
	1. En este caso, debemos ejecutar primero el script `yolo/scripts/zip_to_train.py`, el cual se encargará de crear un archivo comprimido con el conjunto de datos, el cual se guardará en la carpeta `yolo/v11/zip`.
	2. Luego, subimos el archivo a Google Drive, le cambiamos la visibilidad a `Anyone with the link can view` y copiamos el ID del archivo comprimido, el cual se encuentra en la URL del mismo. Este enlace lo pegamos en la sección correspondiente del Jupyter Notebook `yolo/v11/notebooks/colab/g_train.ipynb` para poder descargar el archivo comprimido en Google Colab.
	3. Seleccionamos el entorno de ejecución acorde a nuestra disponibilidad. Puedes utilizar de forma gratuita una GPU Tesla T4 de NVIDIA por alrededor de 5 h diarias, o comprar 100 créditos (que cuestan $10 al momento de redactar esta guía) de la plataforma para poder usarlo por más tiempo y/o utilizar mejores GPU. En nuestro caso, empleamos una GPU Tesla L4 de NVIDIA, la cual consumió alrededor de 6 créditos por entrenar un modelo completo.
	4. Ejecutamos las secciones del Jupyter Notebook `yolo/v11/notebooks/colab/g_train.ipynb`, omitiendo la sección antes mencionada relacionada con la descompresión del archivo comprimido. Este Jupyter Notebook utiliza la librería [Ultralytics](../libraries/python.es.md#ultralytics-yolo) para realizar el entrenamiento del modelo y guarda los pesos en la carpeta `yolo/v11/runs/g`.
	5. Una vez finalizado el entrenamiento, se puede descargar el archivo comprimido con los pesos del modelo desde Google Drive y descomprimirlo en la carpeta `yolo/v11/runs/g` de forma local.
3. **Inferencia**: Ejecutamos el script `yolo/scripts/test.py` para realizar la inferencia del modelo entrenado y evaluar el rendimiento del modelo con imágenes que no ha visualizado con anterioridad. Este script genera imágenes con las inferencias realizadas por el modelo, donde se muestran los cuadros delimitadores y las etiquetas de los objetos detectados.
4. **ONNX**: Ejecutamos el script `yolo/scripts/export.py`, y pasamos como formato del modelo `onnx`, el cual es un formato abierto empleado para representar modelos de Machine Learning de forma interoperable entre distintos frameworks, herramientas, entre otros [[2](#onnx)].
5. **Limpieza**: Finalmente, ejecutamos el script `yolo/scripts/after_training.py` para eliminar la carpeta `yolo/dataset/g/organized/val`, ya que esta no serán necesaria para los próximos pasos. Además, moverá el contenido de la carpeta `yolo/dataset/g/organized/train/images` al subdirectorio en `hailo/suite/train`, para posteriormente ser eliminada la primera. Así mismo, para que el modelo pueda ser convertido a un formato compatible con el Hailo 8, moverá los pesos de formato `ONNX` con mejor resultado correspondiente al modelo.

> [!TIP]
> En el caso de emplear Google Colab y que se desconecte la sesión del entorno de ejecución durante el entrenamiento del modelo, se puede retomar el mismo, al modificar la ruta del modelo o el nombre del modelo a emplear en la función `train_model` del Notebook, por la ruta donde se guardó los mejores pesos del entrenamiento, en nuestro caso: `g_to_train/yolo/v11/runs/m/weights/best.pt`.

<!-- github-only-start -->
<p align="center">
   Vista frontal de la GPU Tesla L4 de NVIDIA
   <br>
   <i>Vista frontal de la GPU Tesla L4 de NVIDIA</i>
</p>
<!-- github-only-end -->

<!-- mkdocs-only-start
<div class="hcenter">
   <img src="/assets/images/components/nvidia-l4.png" 
alt="Vista frontal de la GPU Tesla L4 de NVIDIA" class="component-image">
    <i>Vista frontal de la GPU Tesla L4 de NVIDIA</i>
</div>
mkdocs-only-end -->

> [!IMPORTANT]
> Durante esta sección se menciona la versión 11 de YOLO, pero, de la misma forma que se menciona el dataset **G** a fines didácticos, se puede utilizar cualquier versión de YOLO, así como cualquier dataset, ya que el proceso es el mismo. Sin embargo, se recomienda utilizar la versión 11 de YOLO, debido a que es la más reciente y cuenta con mejoras significativas en comparación con versiones anteriores.

## Conversión del Modelo {:#model-conversion}

Para la conversión del modelo a un formato compatible con el Hailo 8, requerimos de Docker (mas no es imprescindible), para crear un contenedor con todos los paquetes necesarios para su correcto funcionamiento.

<!-- github-only-start -->
<p align="center">
	Logo de Docker
	<br>
	<i>Logo de Docker</i>
</p>
<!-- github-only-end -->

<!-- mkdocs-only-start
<div class="hcenter">
    <img src="/assets/images/logo/docker.png" alt="Logo de Docker" 
class="logo--3rd-party">
    <i>Logo de Docker</i>
</div>
mkdocs-only-end -->

Al momento de la instalación de la AI HAT+, ejecutamos el comando `hailortcli fw-control identify`, donde pudimos notar la siguiente línea:

```
Firmware Version: 4.20.0 (release,app,extended context switch buffer)
```

Como podemos observar, en nuestro caso, la versión del firmware es 4.20.0, por lo que debemos asegurarnos de que el Dataflow Compiler, sea compatible con esta versión. Por ejemplo, debido a un cambio en el Dataflow Compiler para la versión 3.31.0, donde se emplean mecanismos distintos para la detección del error de forma predeterminada, las versiones viejas (previas a la 4.21.0) del HailoRT no serán capaces de ejecutar archivos HEF compilados por la nueva versión del DataFlow Compiler [[3](#2025-04-hailo)]. Recomendamos revisar la [Tabla de Compatibilidad](https://hailo.ai/developer-zone/documentation/hailo-sw-suite-2025-04/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), para así poder tener conocimiento de las versiones de los paquetes que debemos instalar para que todos sean compatibles entre sí.

Primeramente, visitamos la página oficial de Hailo, en el cual debemos crearnos una cuenta, iniciar sesión y luego nos dirigimos al apartado de desarrolladores. Dentro de esta sección, seleccionamos el apartado de descargas de software, y descargamos los siguientes paquetes necesarios [[1](#custom-dataset-medium)]:

- HailoRT, para la arquitectura donde está siendo ejecutado el Docker (en nuestro caso, `amd64`). Versión recomendada: 4.20.0.
- Paquete de Python (whl) de HailoRT, para la arquitectura donde está siendo ejecutado el Docker (en nuestro caso, x86_64), y la versión de Python del contenedor (de no ser modificado, debe ser la versión 3.10). Versión recomendada: 4.20.0.
- Hailo Dataflow Compiler, para la arquitectura donde está siendo ejecutado el Docker (en nuestro caso, `x86_64`). Versión recomendada: 3.30.0.

> [!IMPORTANT]
> En el caso de emplear una GPU NVIDIA para la optimización del formato `.har`, también debemos instalar el [NVIDIA Container Toolkit](https://docs.nvidia.com/datacenter/cloud-native/container-toolkit/install-guide.html)

> [!IMPORTANT]
> En el caso de no conseguir uno de los paquetes, en el portal para descargar software de Hailo, se tienen dos formas para buscar los paquetes: `Latest releases` (o últimas versiones), y `Archive` (o archivados); el primero de ellos es el predeterminado. De no conseguir el respectivo paquete en `Latest releases`, este probablemente esté en `Archive`.

Posteriormente, cambiamos de nuevo el directorio actual:

- Si contamos con GPU, al directorio `hailo/suite/dockerfiles/gpu`, con el comando:
    ```bash
    cd hailo/suite/dockerfiles/gpu
    ```
- En el caso de no contar con GPU, al directorio `hailo/suite/dockerfiles/no-gpu`.
    ```bash
    cd hailo/suite/dockerfiles/no-gpu
    ```

En ambos casos, debe existir un archivo `Dockerfile`, indiferentemente de la carpeta en la que nos encontramos.

Para crear la imagen de Docker, ejecutamos el siguiente comando:

```bash
docker build -t hailo_compiler:v0 .
```

Esperamos a que se instalen todas las dependencias necesarias y la imagen del contenedor Docker esté lista.

Posteriormente, inicializamos el contenedor Docker:

- En el caso de contar con GPU:
    ```bash
    docker run -it --name compile_onnx_file --gpus all --ipc=host -v {path}:/home/hailo/shared hailo_compiler:v0
    ```

- En el caso de no contar con GPU:
    ```bash
    docker run -it --name compile_onnx_file --ipc=host -v {path}:/home/hailo/shared hailo_compiler:v0
    ```

> [!NOTE]
> Sustituimos `path` por la ruta absoluta de la carpeta `hailo/suite`.

Dentro del contenedor, nos movemos al directorio `/home/hailo/shared/libs`:

```bash
cd /home/hailo/shared/libs
```

En el mismo terminal, creamos un entorno virtual para Python:

```bash
python -m venv .venv
source .venv/bin/activate
```

Ahora instalamos los paquetes anteriormente descargados, que actualmente se encuentran en la carpeta `hailo/suite/libs`. Para la versión que descargamos, ejecutamos el siguiente comando:

```bash
dpkg -i hailort_4.20.0_amd64.deb
pip install  hailort-4.20.0-cp310-cp310-linux_x86_64.whl
pip install hailo_dataflow_compiler-3.30.0-py3-none-linux_x86_64.whl
```

Realizamos un clone del siguiente repositorio de GitHub que contiene todo lo necesario para la conversión del modelo de formato `ONNX` a `HEF`:

```bash
git clone https://github.com/hailo-ai/hailo_model_zoo.git
```

Sin embargo, en nuestro caso, como requerimos de la versión v2.14, el comando sería el siguiente:

```bash
git clone -b v2.14 https://github.com/hailo-ai/hailo_model_zoo.git
```

Ahora nos movemos del directorio actual al correspondiente del repositorio `hailo-model-zoo`:

```bash
cd hailo_model_zoo
```

Instalamos todas las dependencias requeridas:

```bash
pip install -e .
```

> [!WARNING]
> En el caso de obtener un error similar a:
> ```bash
> ERROR: pip's dependency resolver does not currently take into account all the packages that are installed. This behaviour is the source of the following dependency conflicts. 
> tensorflow 2.12.0 requires numpy<1.24,>=1.22, but you have numpy 2.2.6 which is incompatible. 
> hailo-dataflow-compiler 3.30.0 requires numpy==1.23.3, but you have numpy 2.2.6 which is incompatible.
> ```
> Debemos modificar el archivo `setup.py` que se encuentra dentro del repositorio, y en la línea 44, dentro de la función `main`, sustituimos `"numpy"` por `"numpy==1.23.3"`, así como en la línea 46, sustituimos `"scipy"` por `"scipy==1.9.3"`. Reintentamos el comando:
> ```bash
> pip install -e .
> ```

Evaluamos si los paquetes se han instalado correctamente con el siguiente comando:

```bash
hailomz --version
```

Ahora modificamos el archivo de configuración del modelo, en el campo `classes`, estableciendo el número de clases con el que se ha entrenado el mismo (para el modelo **G** sería 1):

```bash
sudo nano hailo_model_zoo/cfg/postprocess_config/yolov11n_nms_config.json
```

Establecemos la variable de entorno `USER` como Hailo:

```bash
export USER=hailo
```

Ahora, para convertir el modelo a un formato compatible con el Hailo 8, ejecutamos los siguientes comandos:

- Primero, parseamos el modelo:
    ```bash
    hailomz parse --ckpt ~hailo/shared/v11/g/best.onnx --hw-arch hailo8 yolov11n
    mv yolov11n.har g_parsed.har
    ```

- Segundo, optimizamos el modelo:
    ```bash
    hailomz optimize --har g_parsed.har --classes 2 --calib-path ~hailo/shared/train --hw-arch hailo8 yolov11n
    mv yolov11n.har g_optimized.har
    ```

- Finalmente, compilamos el modelo:
    ```bash
    hailomz compile --har g_optimized.har --hw-arch hailo8 yolov11n
    mv yolov11n.hef g_compiled.hef
    ```

Esperamos a que se complete el anterior paso, y ya tendríamos nuestro modelo personalizado y compatible con el Hailo 8.

Para mover todos los archivos generados en el directorio `hailo/suite/libs/hailo_model_zoo` a la carpeta con los pesos del modelo correspondiente, ejecutamos el script `yolo/scripts/after_hailo_compilation.py`.

Por último, para salir del contenedor Docker, ejecutamos el siguiente comando:

```bash
exit
```

## Prueba del Modelo

Después de haber completado todos los pasos anteriores, nos movemos a la carpeta `hailo/suite/libs`, y clonamos el siguiente repositorio:

```bash
git clone https://github.com/hailo-ai/hailo-rpi5-examples.git
```

Nos cambiamos de nuevo de carpeta, ahora a `hailo-rpi5-examples`, con el siguiente comando:

```bash
cd hailo-rpi5-examples
```

Ejecutamos el siguiente comando para instalar todas las dependencias necesarias:

```bash
./install.sh
```

Ahora, cada vez que abramos un nuevo terminal, ejecutamos el siguiente comando:

```bash
source setup_env.sh
```

En este momento, ya podemos probar tanto que todo esté funcionando correctamente, como la precisión del modelo:

- Si contamos con una cámara con puerto CSI compatible con la Raspberry Pi, después de conectarlo, ejecutamos el siguiente comando:
    ```bash
    python basic_pipelines/detection.py --input rpi --labels-json ../labels/g.json --hef-path ../../v11/runs/g/weights/compiled.hef
    ```

- Si no contamos con una cámara, podemos utilizar el siguiente comando para probar el modelo con una imagen de prueba:
    ```bash
    python basic_pipelines/detection.py --input {imagen} --labels-json ../labels/g.json --hef-path ../../v11/runs/g/weights/compiled.hef
    ```

> [!NOTE]
> Sustituimos `imagen` por la ruta de la imagen a probar.

Esto abrirá una ventana con la cámara, donde se mostrarán los cuadros delimitadores y las etiquetas de los objetos detectados. Si todo está funcionando correctamente, deberíamos ver los objetos detectados en tiempo real.

# Referencias

1. d'Oleron, L. (23 de abril de 2025). *Custom dataset with Hailo AI Hat, Yolo, Raspberry PI 5, and Docker*. Medium. <a id="custom-dataset-medium" href="https://pub.towardsai.net/custom-dataset-with-hailo-ai-hat-yolo-raspberry-pi-5-and-docker-0d88ef5eb70f">https://pub.towardsai.net/custom-dataset-with-hailo-ai-hat-yolo-raspberry-pi-5-and-docker-0d88ef5eb70f</a>

2. *ONNX*. (2025). ONNX. <a id="onnx" href="https://onnx.ai/">https://onnx.ai/</a>

3. *2025-04 | Hailo*. (2025). Hailo. <a id="2025-04-hailo" href="https://hailo.ai/developer-zone/documentation/hailo-sw-suite-2025-04/?sp_referrer=suite/suite_changelog.html">https://hailo.ai/developer-zone/documentation/hailo-sw-suite-2025-04/?sp_referrer=suite/suite_changelog.html</a>

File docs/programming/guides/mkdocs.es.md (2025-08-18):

# Guía de MkDocs

<!-- github-only-start -->
<p align="center">
	Logo de MkDocs
	<br>
	<i>Logo de MkDocs</i>
</p>
<!-- github-only-end -->

<!-- mkdocs-only-start
<div class="hcenter">
    <img src="/assets/images/logo/mkdocs.png" alt="Logo de MkDocs" 
class="logo--3rd-party">
    <i>Logo de MkDocs</i>
</div>
mkdocs-only-end -->

En la presente sección se presenta una guía para instalar MkDocs y servir la documentación desarrollada con la misma librería, una herramienta de documentación estática que permite generar sitios web a partir de archivos Markdown.

## Instalación

Para instalar MkDocs, es necesario tener `Python` y `pip` instalados en tu sistema. Así mismo, requerimos de todas las dependencias del proyecto. Para simplificar el proceso de instalación, hemos creado un archivo `requirements.txt` que contiene todas las dependencias necesarias para el proyecto.

Puedes crear un entorno virtual de Python, instalar MkDocs y las dependencias del proyecto ejecutando el siguiente comando en la terminal:

- Si el sistema operativo es Windows:

```cmd
python -m venv .venv
./.venv/Scripts/activate
pip install -r requirements.txt
```

- Si el sistema operativo es Linux o macOS:

```bash
python3 -m venv .venv
source .venv/bin/activate
pip install -r requirements.txt
```

## Servir la Documentación

Una vez que hayas instalado MkDocs y las dependencias del proyecto, puedes servir la documentación localmente ejecutando el siguiente comando en la terminal:

```bash
mkdocs serve
```

> [!IMPORTANT]
> En el caso de querer servir la documentación desde otra terminal, es necesario activar el entorno virtual de Python nuevamente, ya que MkDocs depende de las dependencias instaladas en el entorno virtual de Python. Esto se puede realizar con el siguiente comando:
> - Si el sistema operativo es Windows:
> ```cmd
> .env\Scripts\activate
> ```
> 
> - Si el sistema operativo es Linux o macOS:
> ```bash
> source .venv/bin/activate
> ```

Aunque si deseas simplificar el proceso, puedes ejecutar directamente el archivo `serve.bat` en Windows o `serve.sh` en Linux o macOS, que se encargará de activar el entorno virtual y servir la documentación automáticamente.

## Despliegue

Para desplegar la documentación en GitHub Pages, puedes utilizar el siguiente comando:

```bash
mkdocs gh-deploy
```

> [!NOTE]
> Este comando creará una rama `gh-pages` en tu repositorio de GitHub y desplegará la documentación en esa rama. Asegúrate de que tu repositorio esté configurado para utilizar GitHub Pages desde la rama `gh-pages`.

> [!IMPORTANT]
> Este comando solamente servirá si el repositorio al que quieres crear la rama no es el repositorio oficial del Team Steel Bot, es decir, un fork del mismo, ya que los usuarios externos al proyecto no tienen los permisos necesarios para realizar cualquier tipo de modificación en el repositorio antes mencionado.

Sin embargo, para simplificar el proceso de despliegue, puedes ejecutar directamente el archivo `deploy.bat` en Windows o `deploy.sh` en Linux o macOS, que se encargará de desplegar la documentación automáticamente. En nuestro caso, este `.bat` o `.sh` se encargará de desplegar la documentación a dicha rama tanto para el repositorio remoto oficial público como para nuestro repositorio de desarrollo interno.

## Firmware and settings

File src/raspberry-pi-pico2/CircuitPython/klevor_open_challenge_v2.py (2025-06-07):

import board
import pwmio
import busio
import math
import time
import adafruit_vl53l0x
import digitalio
from adafruit_motor import servo
from adafruit_bno08x.i2c import BNO08X_I2C
from adafruit_bno08x import (BNO_REPORT_GYROSCOPE, BNO_REPORT_ROTATION_VECTOR)
import asyncio

# ---------- CONSTANTS ----------

# ToF sensors I2C bus
I2C_BUS0 = busio.I2C(board.GP1, board.GP0) 

# Gyroscope I2C bus
I2C_BUS1 = busio.I2C(board.GP27, board.GP26) # Used for Gyroscope

# General configuration
MOVEMENT_MODE = True
DEBUG_MODE = False

# Movement delay
MOVEMENT_DELAY = 0.05

# Speed Values
ROBOT_SPEED_FORWARD_NORMAL = 0.3
ROBOT_SPEED_TURN = 0.2
ROBOT_SPEED_STOP = 0

# Steering servo configuration
TURNING_VALUE = 30 

# ToF Sensors pins and configuration
FRONT_SENSOR_XSHUT_PIN = board.GP5
DIAGONAL_LEFT_FRONT_SENSOR_XSHUT_PIN = board.GP4
DIAGONAL_RIGHT_FRONT_SENSOR_XSHUT_PIN = board.GP22
LEFT_MIDDLE_SENSOR_XSHUT_PIN = board.GP7
RIGHT_MIDDLE_SENSOR_XSHUT_PIN = board.GP28
LEFT_REAR_SENSOR_XSHUT_PIN = board.GP12
RIGHT_REAR_SENSOR_XSHUT_PIN = board.GP16
BACK_SENSOR_XSHUT_PIN = board.GP17
TOF_SENSORS_XSHUT_PINS = [FRONT_SENSOR_XSHUT_PIN, DIAGONAL_LEFT_FRONT_SENSOR_XSHUT_PIN, DIAGONAL_RIGHT_FRONT_SENSOR_XSHUT_PIN,
              LEFT_MIDDLE_SENSOR_XSHUT_PIN, RIGHT_MIDDLE_SENSOR_XSHUT_PIN, LEFT_REAR_SENSOR_XSHUT_PIN,
              RIGHT_REAR_SENSOR_XSHUT_PIN, BACK_SENSOR_XSHUT_PIN]
TOF_FRONT_SENSOR = 0
TOF_LEFT_MIDDLE_SENSOR = 3
TOF_RIGHT_MIDDLE_SENSOR = 4
TOF_BACK_MIDDLE_SENSOR = 7
TOF_SENSORS_NEW_I2C_ADDRESSES = [0x30, 0x31, 0x32, 0x33, 0x34, 0x35, 0x36, 0x37]
TOF_SENSOR_DELAY=0.1
TOF_SENSOR_SHORT_DELAY=0.05

# Start button pins and delay
START_BUTTON_PIN_IN = board.GP14
START_BUTTON_PIN_OUT = board.GP15 
START_BUTTON_DELAY = 0.1

# Distance Thresholds
TARGET_DISTANCE_FORWARD = 80 # When the front sensor distance measured is lower than this, the robot should be starting to approach a turning section
SENSOR_DIFFERENCE_SIDEWAYS = 80 # One of the side sensors detects a distance lower than this value, it is usually compared to another sensor to confirm the distance
TOO_FAR_SIDEWAYS = 200 # This value is pretty much explained above

# Steering commands
STEERING_LEFT_COMMAND = -1
STEERING_MIDDLE_COMMAND = 0
STEERING_RIGHT_COMMAND = 1

# Servo pins and configuration
SERVO_PIN = board.GP20
SERVO_PWM_CONFIGURATION = pwmio.PWMOut(SERVO_PIN, duty_cycle=0, frequency=50)
SERVO_DIRECTION = servo.Servo(SERVO_PWM_CONFIGURATION, actuation_range=180, min_pulse=500, max_pulse=2500)
SERVO_DIRECTION_CENTER = 82
SERVO_DIRECTION.angle = SERVO_DIRECTION_CENTER #This angle actually takes our steering to go forward

# Motor pins and configuration
ESC_MOTOR_PIN = board.GP21
ESC_PWM_Configuration = pwmio.PWMOut(ESC_MOTOR_PIN, duty_cycle=0, frequency=50)
ESC = servo.ContinuousServo(ESC_PWM_Configuration, min_pulse=1000, max_pulse=2000)

# ---------- VARIABLES ----------

# Gyroscope state and turn counter (initialized to avoid issues)
bno = None
yaw_deg = 0.0 
roll_deg = 0.0
pitch_deg = 0.0
last_raw_yaw = None # Stores the raw yaw from previous reading for unwrapping
turns = 0 #Counts each time the robot successfully does a 90-degree turn
last_segment_count = 0 # Helper for counting turns

# List of DigitalInOut objects for XSHUT pins and ToF sensors
vl53l0x_xshut = []
vl53l0x_sensors = []

# Start button
start_button_in = None
start_button_out = None

# ToF sensors measures
tof_sensors_measures = []

# ---------- SETUP ----------

def setup():
    # Initialize Start button
    start_button_out = digitalio.DigitalOut(START_BUTTON_PIN_OUT)
    start_button_in = digitalio.DigitalOut(START_BUTTON_PIN_IN)
    start_button_out.direction = digitalio.Direction.OUTPUT
    start_button_in.direction = digitalio.Direction.IN
    
    try:
        bno = BNO08X_I2C(I2C_BUS1, address=0x4B) # Normally you don't need to force and I2C address, but in our case we had to
        if DEBUG_MODE:
            print("Gyroscope started correctly.")
    except Exception as e:
        if DEBUG_MODE:
            print(f"ERROR, Gyro failed to start: {e}.")
        raise e
    
    # Don't forget to enable these features
    bno.enable_feature(BNO_REPORT_GYROSCOPE)
    bno.enable_feature(BNO_REPORT_ROTATION_VECTOR)
    
    # Initialize VL53L0X XSHUT pins list here
    if DEBUG_MODE:
        print("Initializing XSHUT pins...")
    for pin_obj in TOF_SENSORS_XSHUT_PINS:
        xshut = digitalio.DigitalInOut(pin_obj)
        xshut.direction = digitalio.Direction.OUTPUT
        xshut.value = False # Keep all sensors off initially
        vl53l0x_xshut.append(xshut)
    
    # Small synchronous pause to ensure all sensors are off
    time.sleep(TOF_SENSOR_DELAY) 
    
    if DEBUG_MODE:
        print("Configuring each ToF Sensor...")
    for i, xshut in enumerate(vl53l0x_xshut):
        if DEBUG_MODE:
            print(f"Activating ToF Sensor {i} and re-addressing...")
        xshut.value = True # Activate the current sensor (pull XSHUT high)
        time.sleep(TOF_SENSOR_DELAY) # Short pause for sensor power-up
    
        try:
            # Initialize the sensor, should be at 0x29
            sensor = adafruit_vl53l0x.VL53L0X(I2C_BUS0)
            
            # Change the I2C address of the current sensor to a new unique address
            sensor.set_address(TOF_SENSORS_NEW_I2C_ADDRESSES[i])
            vl53l0x_sensors.append(sensor)
    
            if DEBUG_MODE:
                print(f"Sensor {i} successfully re-addressed to {hex(TOF_SENSORS_NEW_I2C_ADDRESSES[i])} and ACTIVE.")
            
            time.sleep(TOF_SENSOR_SHORT_DELAY) # Small synchronous pause before activating next sensor
        except ValueError as e:
            if DEBUG_MODE:
                print(f"ERROR: No VL53L0X device found for Sensor {i} at address 0x29.")
                print(f"Detailed Error: {e}")
            break # Exit the loop if a sensor fails to initialize
    
    if len(vl53l0x_sensors) != len(TOF_SENSORS_XSHUT_PINS):
        if DEBUG_MODE:
            print("Error: At least one ToF sensor faield to initialize")
        while True:
            time.sleep(1)
    
    if DEBUG_MODE:
        print("Started successful")

# ---------- SENSOR FUNCTIONS ----------

# This function receives the 4 components of the quaternion and calculates the orientation
def quaternion_to_euler_degrees(x, y, z, w):
    # Roll
    sinr_cosp = 2 * (w * x + y * z)
    cosr_cosp = 1 - 2 * (x * x + y * y)
    roll_rad = math.atan2(sinr_cosp, cosr_cosp)

    # Pitch
    sinp = 2 * (w * y - z * x)
    # Clamp the value to avoid domain errors for asin (should be between -1 and 1)
    pitch_rad = math.asin(min(1, max(-1, sinp))) # Clamp value to avoid domain errors for asin

    # Yaw
    siny_cosp = 2 * (w * z + x * y)
    cosy_cosp = 1 - 2 * (y * y + z * z)
    yaw_rad = math.atan2(siny_cosp, cosy_cosp)

    return math.degrees(roll_rad), math.degrees(pitch_rad), math.degrees(yaw_rad)
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

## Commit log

2025-05-07 refactor: separated code by device, and add Raspberry Pi Pico built-in LED script test
2025-05-12 test: added some templates for Pi 5 and Pico 2 serial communication and multiprocessing
2025-05-16 feat: added some content to the main Raspberry Pi 5 and YOLO README.md files
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2025-05-19 doc: improved Hailo 8L model conversion guide on YOLO README.md
    * Improved Hailo 8L model conversion guide on YOLO README.md
    * Added 'frames.py', 'local_streaming_server.py' and 'after_hailo_compilation.py'
2025-05-22 feat: added 'Camera' class that encapsulates all the functionality required for this project
2025-05-23 test: snapshot of major implementation of the Raspberry Pi 5 competition scripts
2025-05-23 test: second snapshot of major implementation of the Raspberry Pi 5 competition scripts
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2025-05-24 doc: added gyroscope and fixed mistakes in READMEs
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2025-05-26 feat: added Raspberry Pi 5 Canakit Case design
    [case-raspberry-pi-5-case-canakit.f3d]
2025-05-27 refactor: major improvement
    * Improve code documentation
    * Added SubLogger class
    * Integrated some methods of the RealtimeTrackerServer and now runs on a separate thread in a separate core if the debug mode is enabled
2025-06-04 feat: added 3d models in .STL format
    [assembled-transmission.stl, axle-transmission.stl, back-knuckle.stl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]
2025-06-04 add: differential 3d model
    [differential v1.stl]
2025-06-05 add: more up-to-date 3d models
    [2nd-floor-mounting.stl, 3rd-floor-mounting.stl, assembled-gear-transmission.stl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]
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2025-06-13 test: added initial version of the WI-FI test on Raspberry Pi Pico 2 to debug new features
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2025-06-13 doc: Prototype 1 corrections
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2025-06-18 refactor: added abstract class for Camera and ImageProcessingQueue
    * Renamed 'ImagesQueue' to 'ImageProcessingQueue'
    * Added abstract class for Camera and ImageProcessingQueue
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2025-06-21 test: second snapshot of an improvement over the Raspberry Pi Pico code
2025-06-21 test: third snapshot of an improvement over the Raspberry Pi Pico code
2025-06-21 test: fourth snapshot of an improvement over the Raspberry Pi Pico code
2025-06-21 test: fifth snapshot of an improvement over the Raspberry Pi Pico code
2025-06-21 test: sixth snapshot of an improvement over the Raspberry Pi Pico code
2025-06-23 test: changed log module due to some issues with the current multiprocessing implementation
2025-06-23 test: changed camera module due to some issues with the current multiprocessing implementation
2025-06-23 test: changed server module due to some issues with the current multiprocessing implementation
2025-06-23 test: changed serial_communication module due to some issues with the current multiprocessing implementation
2025-06-23 test: changed serial_communication module due to some issues with the current multiprocessing implementation (part II)
2025-06-23 test: changed rplidar module due to some issues with the current multiprocessing implementation
2025-06-23 test: changed Hailo class implementation due to some issues with the current multiprocessing implementation
2025-06-23 test: changed ObjectDetector class implementation due to some issues with the current multiprocessing implementation
2025-06-23 test: added some methods to Pilot class to handle the motor speed and servo angle
    * Added some methods to Pilot class to handle the motor speed and servo angle
    * Modified Raspberry Pi Pico libraries according to the new methodology
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2025-06-24 test: improved serial communication sending and receiving logic on both Raspberry Pi 5 and Raspberry Pi Pico 2W
2025-06-25 feat: added Structurizr top-level diagrams of the different processes on the current implementation
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2025-06-26 test: solved some bugs
    * Solved some bugs
    * Added initial version of logger to Raspberry Pi Pico
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2025-06-29 refactor: reformatted code and fix minor typo on Raspberry Pi 5 README.md
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2025-06-29 fix: solved a bug on the servo and ESC motor that prevent some movements
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2025-07-01 refactor: ordered 3d designs and added prototype3's README
    [2nd-floor-mounting.stl, 3rd-floor-mounting.stl, assembled-gear-transmission.stl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]
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2025-07-02 some prototype3's readme corrections.
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2025-07-07 refactor: changed MkDocs theme to Material
    * Changed MkDocs theme to Material, and customized it
    * Added favicon
    * Added MkDocs deploy scripts
2025-07-07 doc: added Raspberry Pi 5 and Raspberry Pi Pico 2W code reference
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2025-07-09 feat: improved MkDocs README.md and added structure for the parts section
    [assembled-gear-transmission.stl, assembled-transmission.stl, axle-transmission.stl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]
2025-07-10 feat: added 2D designs pictures
    [3rd-floor-mounting.stl, assembled-gear-transmission.stl, assembled-transmission.stl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]
2025-07-10 doc: fixed some mistakes in the flowcharts
2025-07-13 feat: added version 2 of the without obstacles challenge flowchart
    # Conflicts:
    # docs/electronic/components/current.md
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2025-07-13 fix: removed some links from the current electronic components .md file
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2025-07-18 refactor: improved mechanical parts section
    [assembled-gear-transmission.stl, assembled-transmission.stl, axle-transmission.stl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]
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2025-07-29 fix: solved flowchart.md broken links and simplified main index
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2025-08-21 feat: added ESC motor and on board LED tests
    * Added ESC motor and on board LED tests
    * Solved some bugs about the implementation of the built-in LED for this Pico model, the Serial Communication, and the pull-down usages (moved to pull-ups)
2025-08-21 feat: added servo test and solved some bugs
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2025-08-21 feat: added github.com/ralvarezdev/rplidar-sdk and github.com/ralvarezdev/hailo-model-zoo as Git submodules
    * Added github.com/ralvarezdev/rplidar-sdk and github.com/ralvarezdev/hailo-model-zoo as Git submodules
    * Moved MicroPython and CircuitPython to legacy folder
2025-08-21 doc: prototype1.md translation and fixes
2025-08-26 test: snapshot of the current local implementation of the BNO08X library for TinyGo
2025-08-26 test: I freaked out with I2C for BNO08x
    I'll give UART a try for this sensor
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2025-08-26 test: it's more stable, even more than in CircuitPython, but it still has some weird errors
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2025-08-28 test: solved some bugs on UART-RVC implementation, added afterResetFn to BNO08X struct, among others
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2025-09-02 fix: solved some bugs on CLIP package
    * Solved some bugs on CLIP package
    * Renamed 'raspberry_pi_5' to 'raspberry-pi-5' and 'raspberry_pi_pico_2w' to 'raspberry-pi-pico-2w'
2025-09-02 test: added get max motor speed value and get max servo direction value
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2025-09-13 test: now, UART mode fails at software reset, but I'll stay with UART-RVC mode
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2025-09-18 feat: added debugging messages to confirm the correct reception of the motor and servo messages
2025-09-18 refactor: upgraded dependencies and modified the order of ESC Motor and Servo feedback messages
2025-09-19 refactor: added start and end messages for motor speed and servo angle commands
2025-09-20 fix: solved another bug on motor stop and servo center
2025-09-20 refactor: added clear servo angle start and end messages channel and motor speed start and end messages channel methods
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2025-09-22 refactor: upgraded dependencies and improved motor speed and servo angle message communication
2025-09-22 refactor: now, the BNO08X updates are being processed even if the button hasn't been pushed
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2025-09-22 refactor: improved servo angle corrections on challenge without obstacles
2025-09-23 test: added center by gyroscope function and splitting pilot handler into multiple structs and functions
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2025-09-26 test: added motor direction time set factor and added dynamic distance change factors based on the motor and servo directions
